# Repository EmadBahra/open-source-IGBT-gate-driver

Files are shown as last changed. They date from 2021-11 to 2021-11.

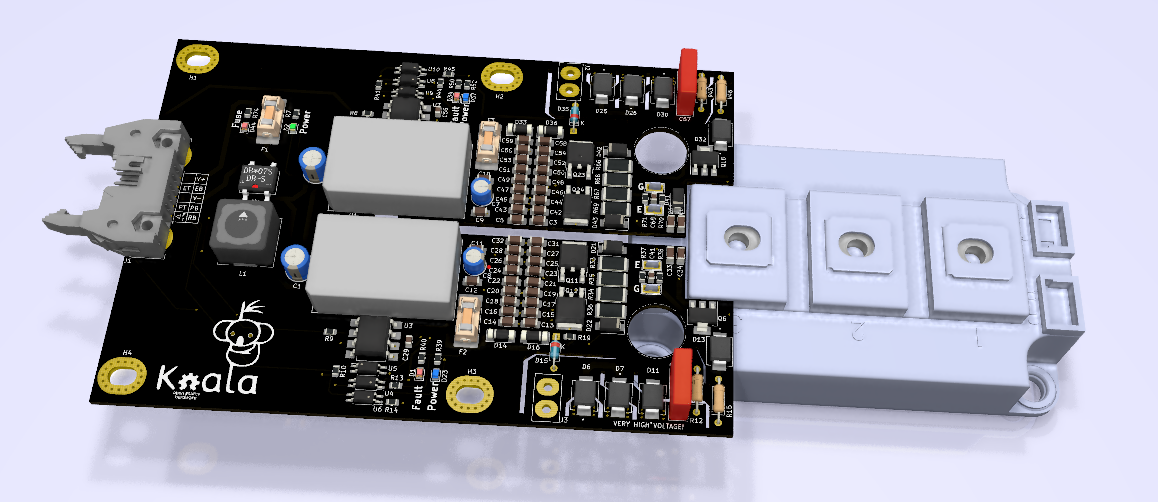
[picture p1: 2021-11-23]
Gate Driver.png

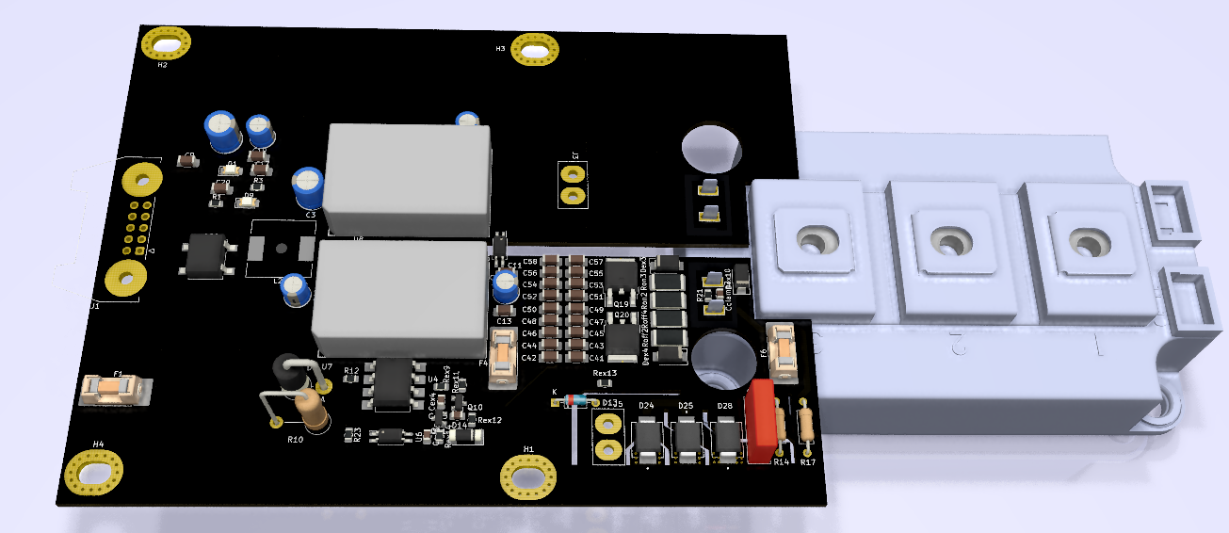
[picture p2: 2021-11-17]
halfway.png

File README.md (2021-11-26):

# Please read Wiki it will be complete ASAP
##  This is a beta version and it's not tested yet, so use it at your own risk under GPL v3 

##  Features
1. Short pulse suppression
2. Under voltage protection
3. Fault soft turn off
4. Active auto reset dynamic VCE clamp
5. Separate Ron and Roff
6. VCE monitoring
7. High side-Low side shoot thought protection (not tested yet)
8. Adjustable VCE protection
9. Mosfet gate clamp

## To add:
1. dynamic short-circuit protection
2. Designing its own converter

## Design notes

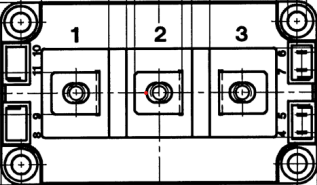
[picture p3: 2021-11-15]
skm200GB.png

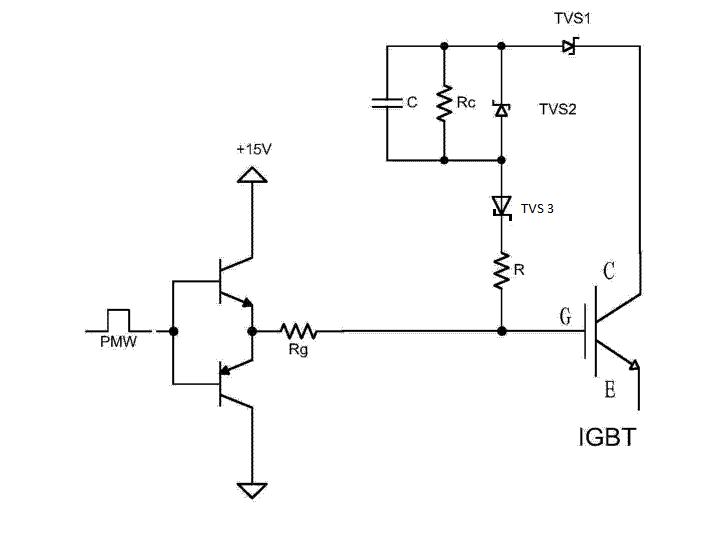
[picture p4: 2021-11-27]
WikiPics/Active Clamping.png

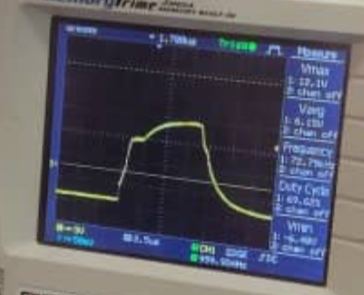
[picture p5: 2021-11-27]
WikiPics/VGE before claming.png

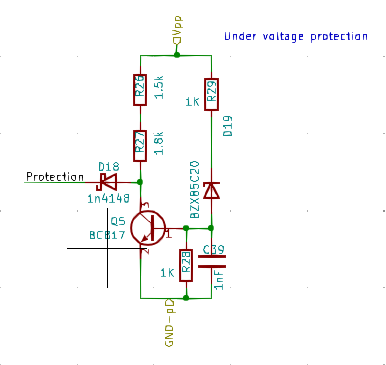
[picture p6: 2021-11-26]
WikiPics/Undervoltage.png

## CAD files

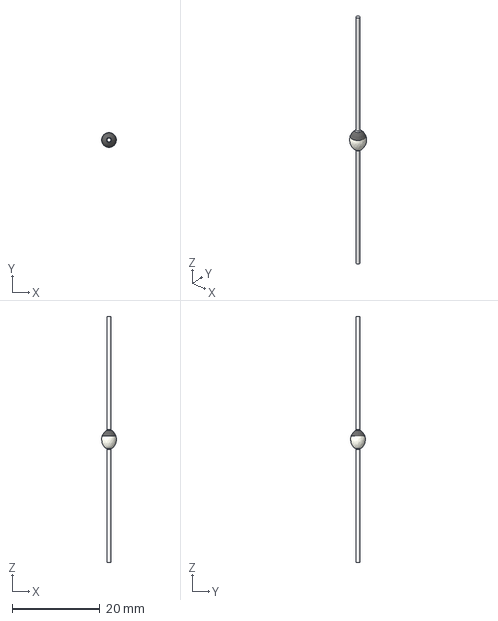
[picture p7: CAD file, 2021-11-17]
SOD-57_BYT62-BY203.stp
3.40 x 3.40 x 56.2 mm

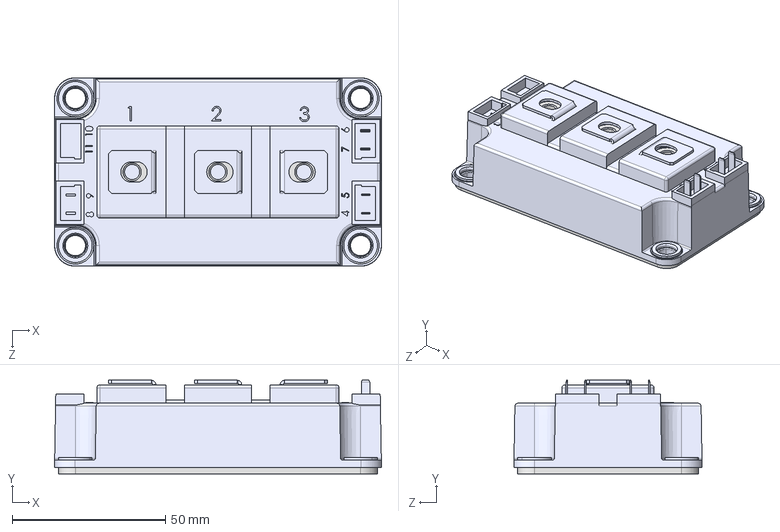
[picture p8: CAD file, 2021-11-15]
SEMIKRON_Semitrans_3_STEP.step
106.6 x 30.5 x 61.4 mm

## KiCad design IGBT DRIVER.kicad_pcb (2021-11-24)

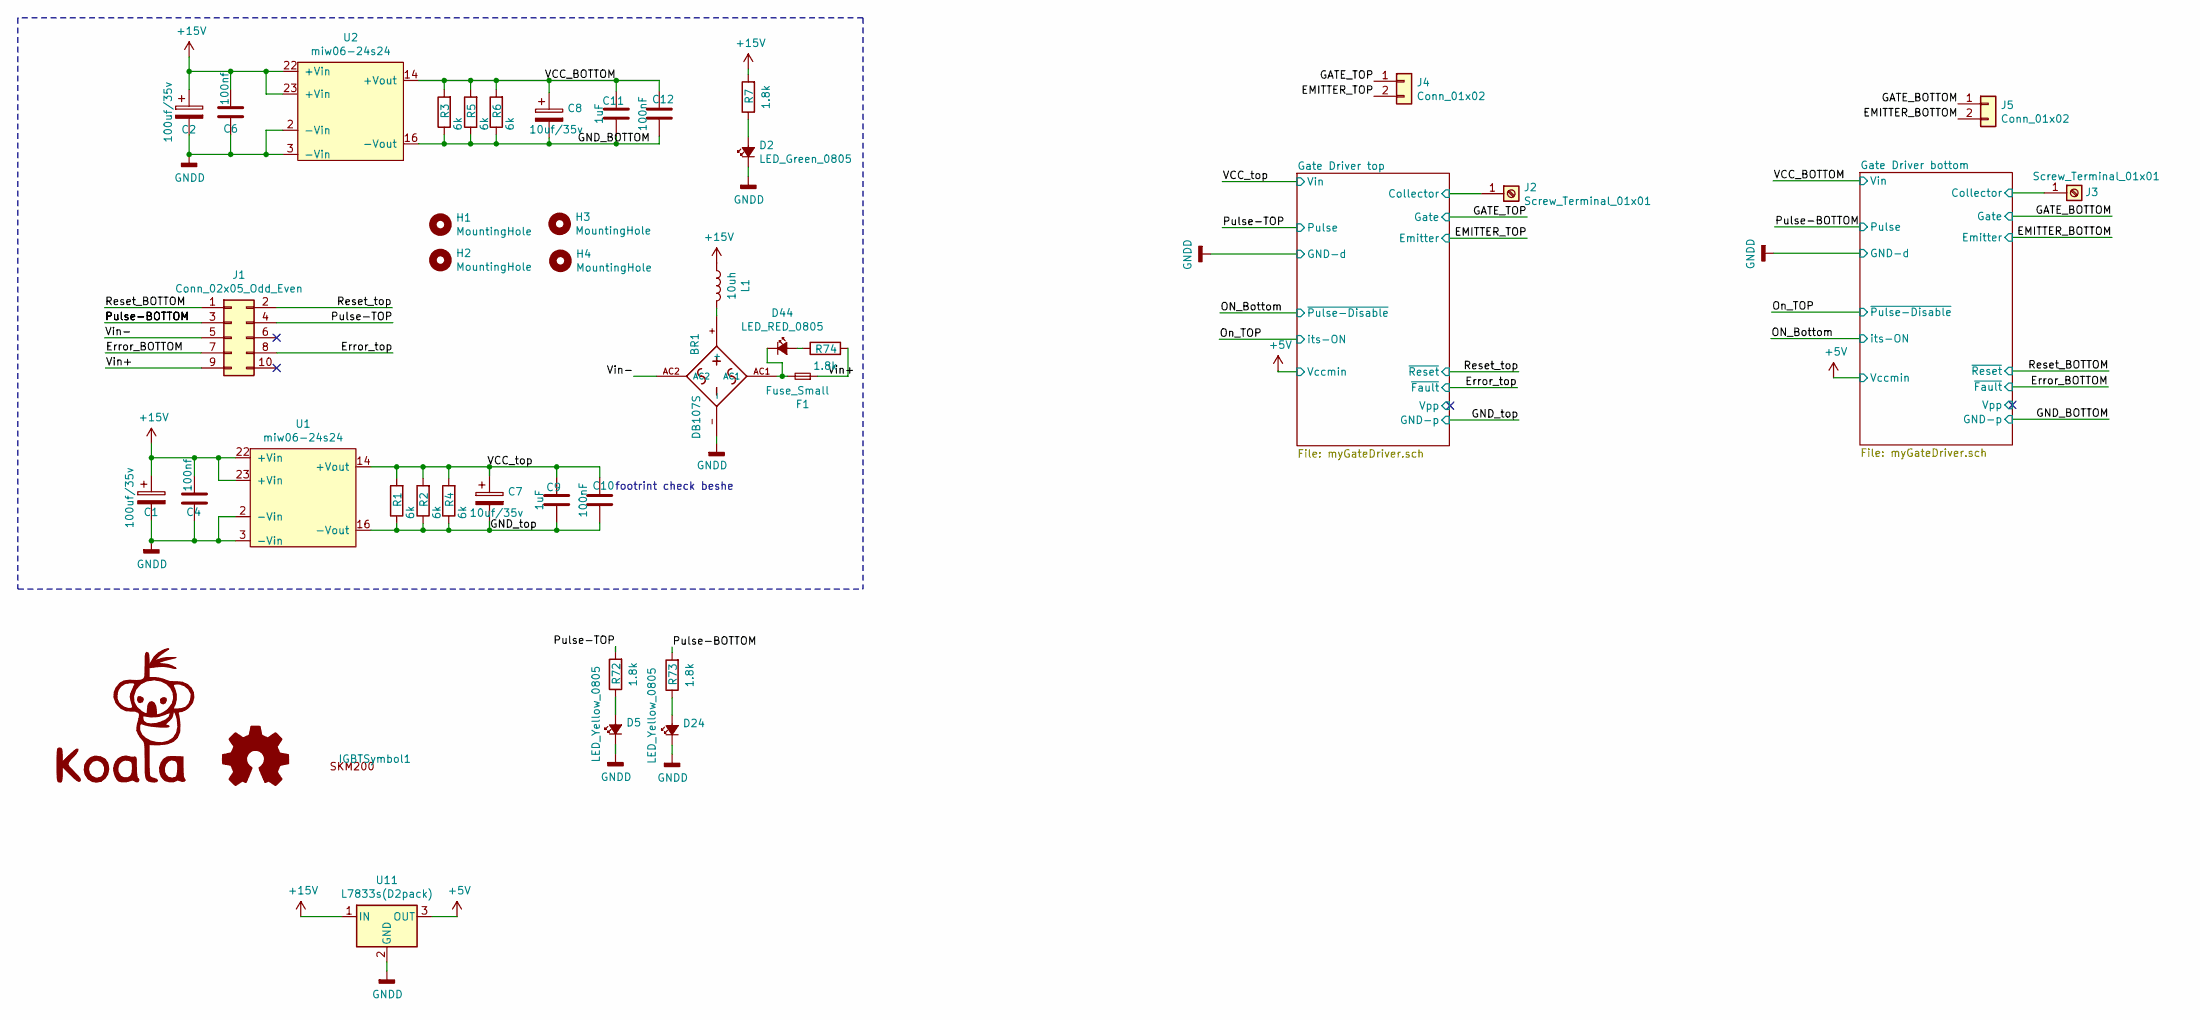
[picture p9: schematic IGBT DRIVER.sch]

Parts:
BR1: DB107S; DIOB_DB107S
C1, C2: 100uf/35v; CP_Radial_D6.3mm_P2.50mm
C4, C6: 100nf; C_1206_3216Metric_Pad1.33x1.80mm_HandSolder
C7, C8: 10uf/35v; CP_Radial_D5.0mm_P2.50mm
C9, C11: 1uF; C_1206_3216Metric_Pad1.33x1.80mm_HandSolder
C10, C12: 100nF; C_1206_3216Metric_Pad1.33x1.80mm_HandSolder
D2: LED_Green_0805
D5, D24: LED_Yellow_0805
D44: LED_RED_0805
F1: Fuse_Small; fuse.holder.1808
G1: LOGO; koalaLogo
H1, H2, H3, H4: MountingHole; MountingHole_4.3x6.2mm_M4_Pad_Via
IGBTSymbol1: SYM_Arrow45_Normal; skm200GB
J1: Conn_02x05_Odd_Even; IDC-Header_2x05-1MP_P2.54mm_Latch_Horizontal
J2, J3: Screw_Terminal_01x01; COOLERI
J4, J5: Conn_01x02; IGBT_Socket
L1: 10uh; L_12x12mm_H6mm
LOGO1: Logo_Open_Hardware_Small; OSHW-Logo_5.7x6mm_SilkScreen
R1, R2, R3, R4, R5, R6: 6k; R_1206_3216Metric
R7, R72, R73, R74: 1.8k; R_0805_2012Metric
U1, U2: miw06-24s24; MIWI06
U11: L7833s(D2pack); TO-263-3_TabPin2

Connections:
+5V: U11.3 (OUT); also elsewhere on the board
+15V: C1.1, C2.1, C4.2, C6.2, L1.1, R7.2, U1.22 (+Vin), U1.23 (+Vin), U2.22 (+Vin), U2.23 (+Vin), U11.1 (IN)
/EMITTER_BOTTOM: J5.2; also elsewhere on the board
/EMITTER_TOP: J4.2; also elsewhere on the board
/Error_BOTTOM: J1.7; also elsewhere on the board
/Error_top: J1.8; also elsewhere on the board
/GATE_BOTTOM: J5.1; also elsewhere on the board
/GATE_TOP: J4.1; also elsewhere on the board
/GND_BOTTOM: C8.2, C11.1, C12.1, R3.1, R5.1, R6.1, U2.16 (-Vout); also elsewhere on the board
/GND_top: C7.2, C9.1, C10.1, R1.1, R2.1, R4.1, U1.16 (-Vout); also elsewhere on the board
/Gate Driver bottom/Collector: J3.1; also elsewhere on the board
/Gate Driver top/Collector: J2.1; also elsewhere on the board
/Pulse-BOTTOM: J1.3, R73.2; also elsewhere on the board
/Pulse-TOP: J1.4, R72.2; also elsewhere on the board
/Reset_BOTTOM: J1.1; also elsewhere on the board
/Reset_top: J1.2; also elsewhere on the board
/VCC_BOTTOM: C8.1, C11.2, C12.2, R3.2, R5.2, R6.2, U2.14 (+Vout); also elsewhere on the board
/VCC_top: C7.1, C9.2, C10.2, R1.2, R2.2, R4.2, U1.14 (+Vout); also elsewhere on the board
/Vin+: F1.1, J1.9, R74.2
/Vin-: BR1.AC2, J1.5
GNDD: BR1.-, C1.2, C2.2, C4.1, C6.1, D2.1 (K), D5.1 (K), D24.1 (K), U1.2 (-Vin), U1.3 (-Vin), U2.2 (-Vin), U2.3 (-Vin), U11.2 (GND); also elsewhere on the board
unnamed: BR1.+, L1.2
unnamed: BR1.AC1, D44.1 (K), F1.2
unnamed: D2.2 (A), R7.1
unnamed: D5.2 (A), R72.1
unnamed: D24.2 (A), R73.1
unnamed: D44.2 (A), R74.1

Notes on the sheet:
footrint check beshe

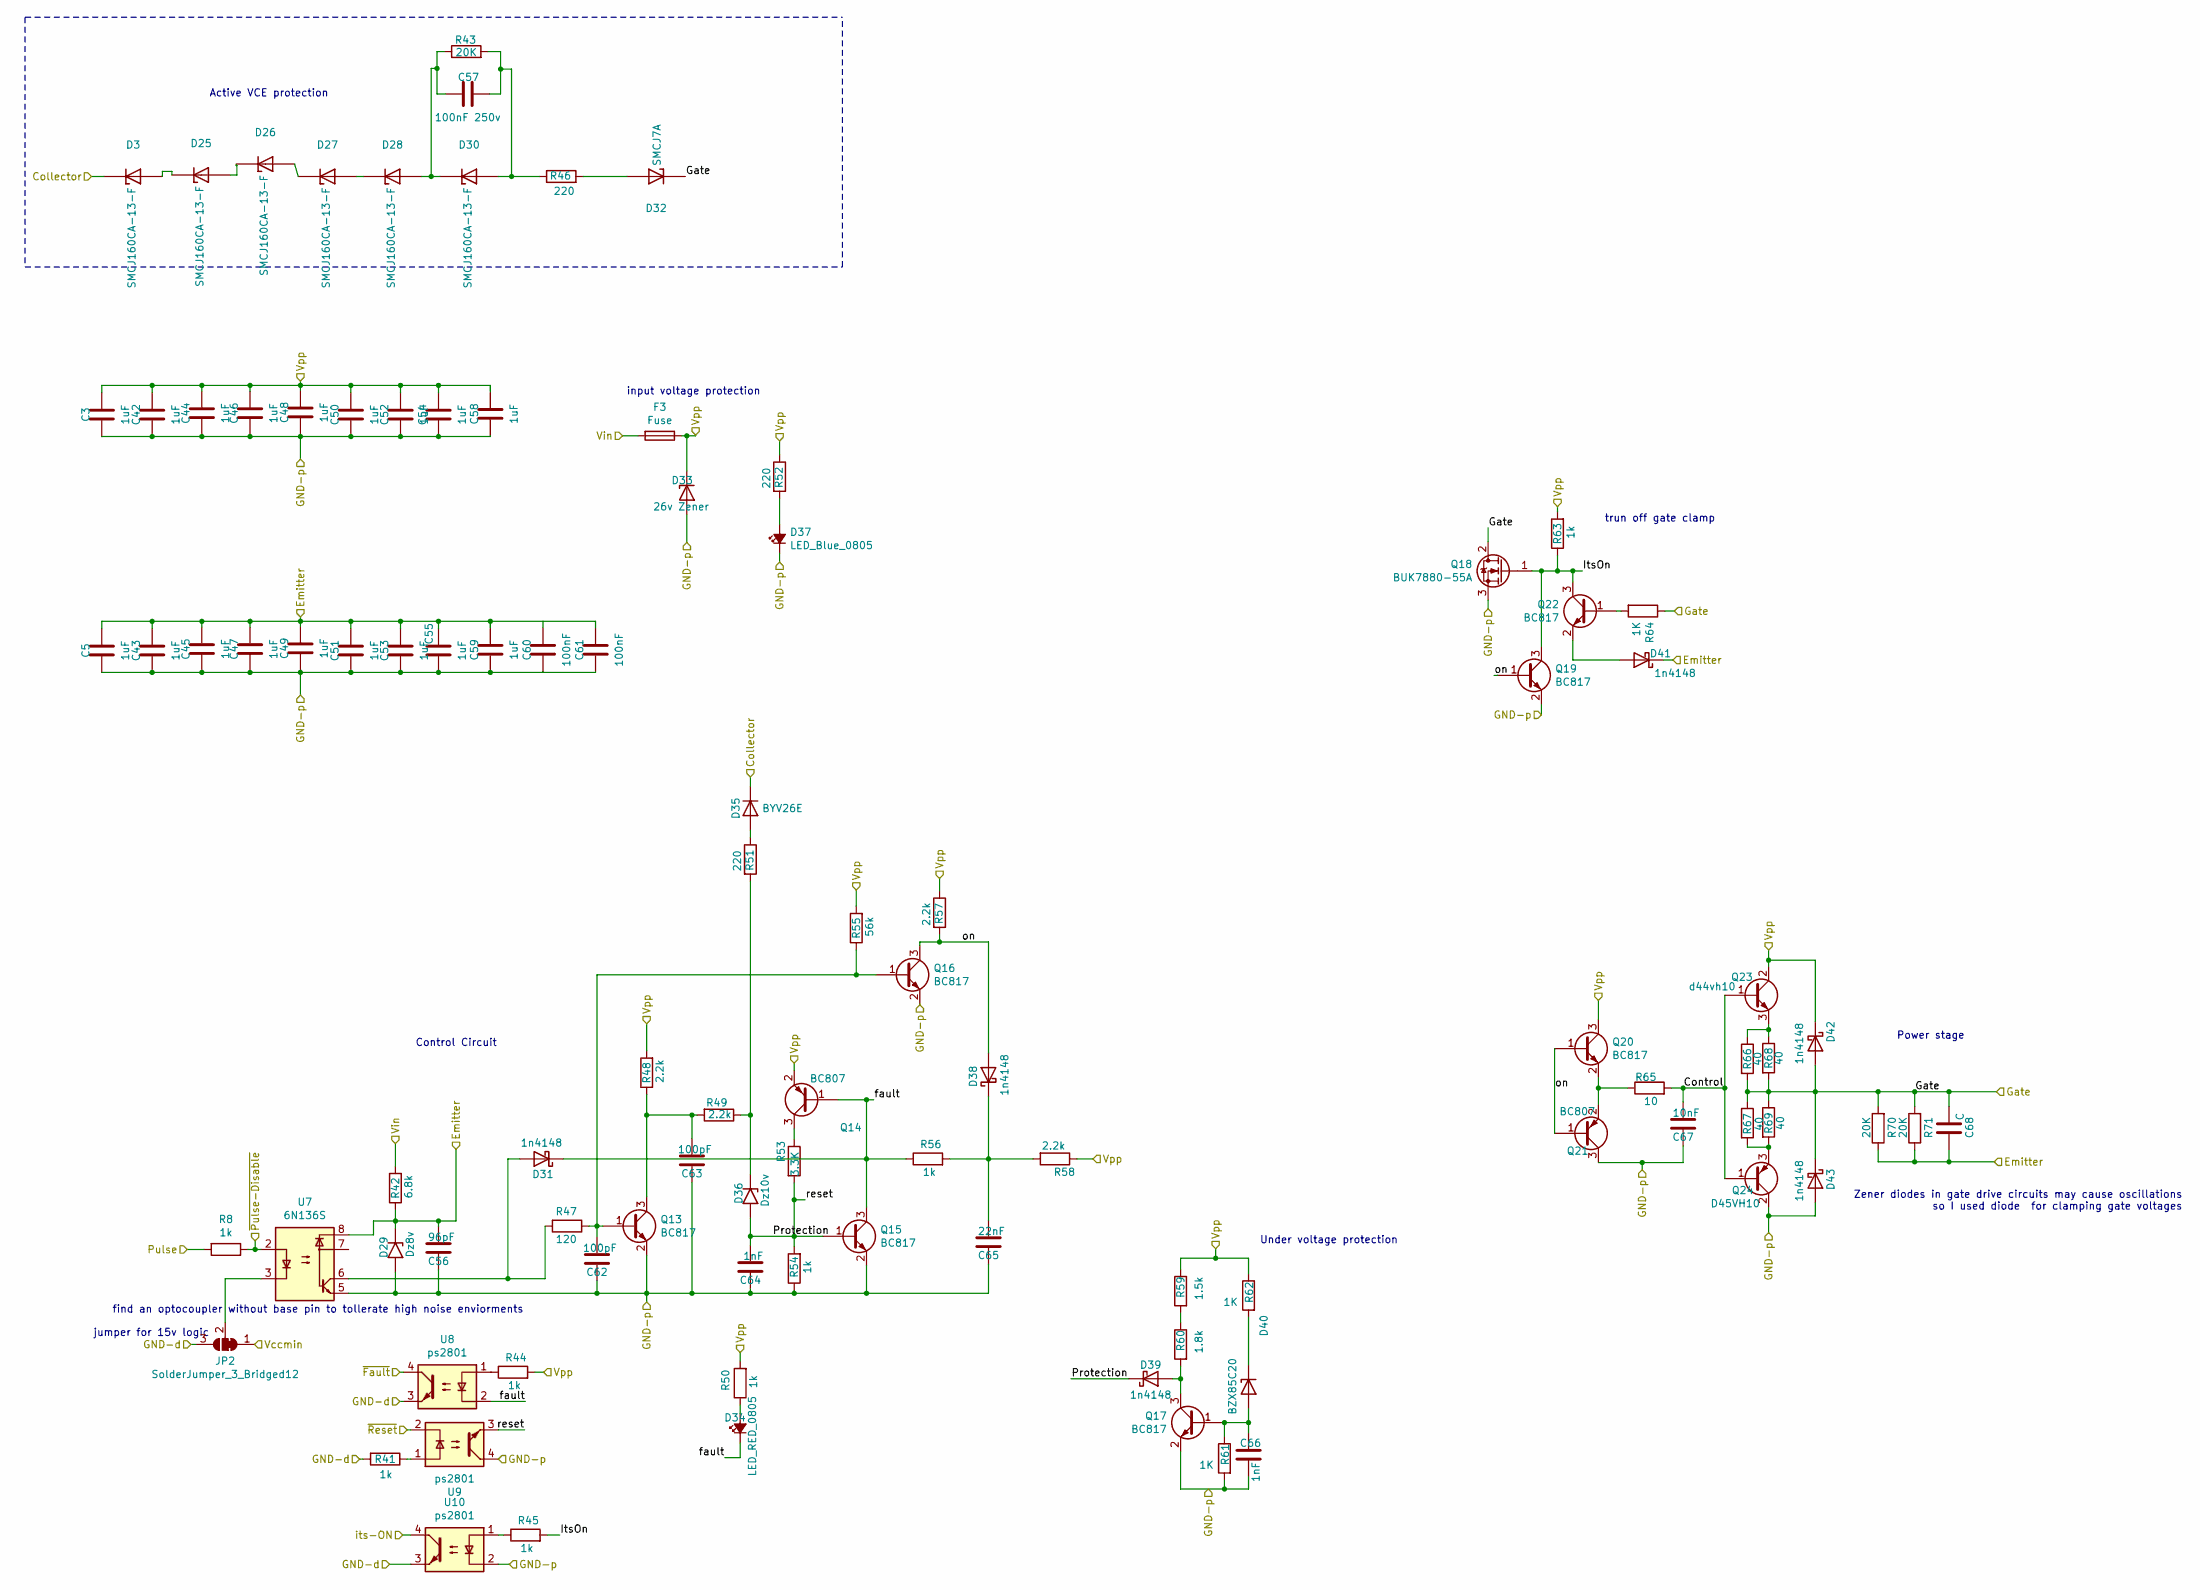
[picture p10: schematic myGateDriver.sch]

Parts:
C13, C14, C15, C16, C17, C18, C19, C20, C21, C22, C23, C24, C25, C26, C27, C28, C31, C32: 1uF; C_1206_3216Metric_Pad1.33x1.80mm_HandSolder
C29: 96pF; C_0805_2012Metric
C30: 100nF 250v; C_Rect_L13.0mm_W4.0mm_P10.00mm_FKS3_FKP3_MKS4
C33, C34: 100nF; C_1206_3216Metric_Pad1.33x1.80mm_HandSolder
C35, C36: 100pF; C_0805_2012Metric
C37: 1nF; C_0805_2012Metric
C38: 22nF; C_0805_2012Metric
C39: 1nF; C_1206_3216Metric_Pad1.33x1.80mm_HandSolder
C40: 10nF; C_0805_2012Metric
C41: C; C_0805_2012Metric
D1: LED_RED_0805
D4, D6, D7, D8, D9, D11: SMCJ160CA-13-F; DIOM7959X250N; PARTREV 5-2
D10: Dz8v; D_MELF
D12, D17, D18, D20, D21, D22: 1n4148; D_SMA
D13: SMCJ7A; DIOM7959X250N; PARTREV 5-2
D14: 26v Zener; D_MELF
D15: BYV26E; D_DO-35_SOD27_P7.62mm_Horizontal
D16: Dz10v; D_MELF
D19: BZX85C20; D_MELF
D23: LED_Blue_0805; LED_BLUE_0805
F2: Fuse; fuse.holder.1808
JP2: SolderJumper_3_Bridged12; SolderJumper-3_P1.3mm_Bridged2Bar12_Pad1.0x1.5mm
Q1, Q3, Q4, Q5, Q7, Q8, Q10: BC817; SOT-23
Q2, Q9: BC807; SOT-23
Q6: BUK7880-55A; SOT-223-3_TabPin2
Q11: d44vh10; TO-252-2
Q12: D45VH10; TO-252-2
R9, R10, R13, R14, R21, R23, R30, R40: 1k; R_0805_2012Metric
R11: 6.8k; R_0805_2012Metric
R12: 20K; R_Axial_DIN0207_L6.3mm_D2.5mm_P10.16mm_Horizontal
R15: 220; R_Axial_DIN0207_L6.3mm_D2.5mm_P10.16mm_Horizontal
R16: 120; R_0805_2012Metric
R17, R18, R24, R25: 2.2k; R_0805_2012Metric
R19, R39: 220; R_0805_2012Metric
R20: 3.3K; R_0805_2012Metric
R22: 56k; R_0805_2012Metric
R26: 1.5k; R_0805_2012Metric
R27: 1.8k; R_0805_2012Metric
R28, R29, R31: 1K; R_0805_2012Metric
R32: 10; R_0805_2012Metric
R33, R34, R35, R36: 40; R_2512_6332Metric
R37, R38: 20K; R_0805_2012Metric
U3: 6N136S; SMDIP-8_W9.53mm
U4, U5, U6: ps2801; SOP-4_4.4x2.6mm_P1.27mm

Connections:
+5V: JP2.1 (A); also elsewhere on the board
/EMITTER_BOTTOM: C14.2, C16.2, C18.2, C20.2, C22.2, C24.2, C26.2, C28.2, C29.2, C32.2, C33.2, C34.2, C41.1, D10.1 (A1), D20.1 (K), R11.1, R37.1, R38.1, U3.8; also elsewhere on the board
/Error_BOTTOM: U4.4; also elsewhere on the board
/GATE_BOTTOM: C41.2, D13.C, D21.2 (A), D22.1 (K), Q6.2 (D), R31.1, R33.2, R34.1, R35.2, R36.1, R37.2, R38.2; also elsewhere on the board
/GND_BOTTOM: C13.1, C14.1, C15.1, C16.1, C17.1, C18.1, C19.1, C20.1, C21.1, C22.1, C23.1, C24.1, C25.1, C26.1, C27.1, C28.1, C29.1, C31.1, C32.1, C33.1, C34.1, C35.1, C36.1, C37.1, C38.1, C39.2, C40.1, D10.2 (A2), D14.2 (A), D22.2 (A), D23.1 (K), Q1.2 (E), Q3.2 (E), Q4.2 (E), Q5.2 (E), Q6.3 (S), Q7.2 (E), Q9.3 (C), Q12.2 (C), R21.1, R28.2, U3.5, U5.4, U6.2; also elsewhere on the board
/Gate Driver bottom/Collector: D4.C, D15.2 (K); also elsewhere on the board
/Gate Driver bottom/Control: C40.2, Q11.1 (B), Q12.1 (B), R32.2
/Gate Driver bottom/ItsOn: Q6.1 (G), Q7.3 (C), Q10.3 (C), R14.2, R30.1
/Gate Driver bottom/Protection: C37.2, D16.2 (A2), D18.1 (K), Q3.1 (B), R20.2, R21.2, U5.3
/Gate Driver bottom/Vpp: C13.2, C15.2, C17.2, C19.2, C21.2, C23.2, C25.2, C27.2, C31.2, D14.1 (K), D21.1 (K), F2.1, Q2.2 (E), Q8.3 (C), Q11.2 (C), R13.2, R17.2, R22.2, R24.1, R25.1, R26.1, R29.1, R30.2, R39.1, R40.2
/Gate Driver bottom/fault: D1.1 (K), D12.1 (K), Q2.1 (B), Q3.3 (C), R23.1, U4.2
/Gate Driver bottom/on: D17.2 (A), Q4.3 (C), Q7.1 (B), Q8.1 (B), Q9.1 (B), R24.2
/ON_Bottom: U6.4; also elsewhere on the board
/On_TOP: R9.1, U3.2; also elsewhere on the board
/Pulse-BOTTOM: R9.2; also elsewhere on the board
/Reset_BOTTOM: U5.2; also elsewhere on the board
/VCC_BOTTOM: F2.2, R11.2; also elsewhere on the board
GNDD: JP2.3 (B), R10.2, U4.3, U6.3; also elsewhere on the board
unnamed: C30.1, D9.A, D11.C, R12.1
unnamed: C30.2, D11.A, R12.2, R15.1
unnamed: C35.2, Q1.1 (B), Q4.1 (B), R16.1, R22.1
unnamed: C36.2, Q1.3 (C), R17.1, R18.2
unnamed: C38.2, D17.1 (K), R23.2, R25.2
unnamed: C39.1, D19.2 (A), Q5.1 (B), R28.1
unnamed: D1.2 (A), R40.1
unnamed: D4.A, D6.C
unnamed: D6.A, D7.C
unnamed: D7.A, D8.C
unnamed: D8.A, D9.C
unnamed: D12.2 (A), R16.2, U3.6
unnamed: D13.A, R15.2
unnamed: D15.1 (A), R19.1
unnamed: D16.1 (A1), R18.1, R19.2
unnamed: D18.2 (A), Q5.3 (C), R27.2
unnamed: D19.1 (K), R29.2
unnamed: D20.2 (A), Q10.2 (E)
unnamed: D23.2 (A), R39.2
unnamed: Q2.3 (C), R20.1
unnamed: Q8.2 (E), Q9.2 (E), R32.1
unnamed: Q10.1 (B), R31.2
unnamed: Q11.3 (E), R33.1, R35.1
unnamed: Q12.3 (E), R34.2, R36.2
unnamed: R10.1, U5.1
unnamed: R13.1, U4.1
unnamed: R14.1, U6.1
unnamed: R26.2, R27.1

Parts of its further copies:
C3, C5, C42, C43, C44, C45, C46, C47, C48, C49, C50, C51, C52, C53, C54, C55, C58, C59: 1uF; C_1206_3216Metric_Pad1.33x1.80mm_HandSolder
C56: 96pF; C_0805_2012Metric
C57: 100nF 250v; C_Rect_L13.0mm_W4.0mm_P10.00mm_FKS3_FKP3_MKS4
C60, C61: 100nF; C_1206_3216Metric_Pad1.33x1.80mm_HandSolder
C62, C63: 100pF; C_0805_2012Metric
C64: 1nF; C_0805_2012Metric
C65: 22nF; C_0805_2012Metric
C66: 1nF; C_1206_3216Metric_Pad1.33x1.80mm_HandSolder
C67: 10nF; C_0805_2012Metric
C68: C; C_0805_2012Metric
D3, D25, D26, D27, D28, D30: SMCJ160CA-13-F; DIOM7959X250N; PARTREV 5-2
D29: Dz8v; D_MELF
D31, D38, D39, D41, D42, D43: 1n4148; D_SMA
D32: SMCJ7A; DIOM7959X250N; PARTREV 5-2
D33: 26v Zener; D_MELF
D34: LED_RED_0805
D35: BYV26E; D_DO-35_SOD27_P7.62mm_Horizontal
D36: Dz10v; D_MELF
D37: LED_Blue_0805; LED_BLUE_0805
D40: BZX85C20; D_MELF
F3: Fuse; fuse.holder.1808
JP1: SolderJumper_3_Bridged12; SolderJumper-3_P1.3mm_Bridged2Bar12_Pad1.0x1.5mm
Q13, Q15, Q16, Q17, Q19, Q20, Q22: BC817; SOT-23
Q14, Q21: BC807; SOT-23
Q18: BUK7880-55A; SOT-223-3_TabPin2
Q23: d44vh10; TO-252-2
Q24: D45VH10; TO-252-2
R8, R41, R44, R45, R50, R54, R56, R63: 1k; R_0805_2012Metric
R42: 6.8k; R_0805_2012Metric
R43: 20K; R_Axial_DIN0207_L6.3mm_D2.5mm_P10.16mm_Horizontal
R46: 220; R_Axial_DIN0207_L6.3mm_D2.5mm_P10.16mm_Horizontal
R47: 120; R_0805_2012Metric
R48, R49, R57, R58: 2.2k; R_0805_2012Metric
R51, R52: 220; R_0805_2012Metric
R53: 3.3K; R_0805_2012Metric
R55: 56k; R_0805_2012Metric
R59: 1.5k; R_0805_2012Metric
R60: 1.8k; R_0805_2012Metric
R61, R62, R64: 1K; R_0805_2012Metric
R65: 10; R_0805_2012Metric
R66, R67, R68, R69: 40; R_2512_6332Metric
R70, R71: 20K; R_0805_2012Metric
U7: 6N136S; SMDIP-8_W9.53mm
U8, U9, U10: ps2801; SOP-4_4.4x2.6mm_P1.27mm

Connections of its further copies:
+5V: JP1.1 (A); also elsewhere on the board
/EMITTER_TOP: C5.2, C43.2, C45.2, C47.2, C49.2, C51.2, C53.2, C55.2, C56.2, C59.2, C60.2, C61.2, C68.1, D29.1 (A1), D41.1 (K), R42.1, R70.1, R71.1, U7.8; also elsewhere on the board
/Error_top: U8.4; also elsewhere on the board
/GATE_TOP: C68.2, D32.C, D42.2 (A), D43.1 (K), Q18.2 (D), R64.1, R66.2, R67.1, R68.2, R69.1, R70.2, R71.2; also elsewhere on the board
/GND_top: C3.1, C5.1, C42.1, C43.1, C44.1, C45.1, C46.1, C47.1, C48.1, C49.1, C50.1, C51.1, C52.1, C53.1, C54.1, C55.1, C56.1, C58.1, C59.1, C60.1, C61.1, C62.1, C63.1, C64.1, C65.1, C66.2, C67.1, D29.2 (A2), D33.2 (A), D37.1 (K), D43.2 (A), Q13.2 (E), Q15.2 (E), Q16.2 (E), Q17.2 (E), Q18.3 (S), Q19.2 (E), Q21.3 (C), Q24.2 (C), R54.1, R61.2, U7.5, U9.4, U10.2; also elsewhere on the board
/Gate Driver top/Collector: D3.C, D35.2 (K); also elsewhere on the board
/Gate Driver top/Control: C67.2, Q23.1 (B), Q24.1 (B), R65.2
/Gate Driver top/ItsOn: Q18.1 (G), Q19.3 (C), Q22.3 (C), R45.2, R63.1
/Gate Driver top/Protection: C64.2, D36.2 (A2), D39.1 (K), Q15.1 (B), R53.2, R54.2, U9.3
/Gate Driver top/Vpp: C3.2, C42.2, C44.2, C46.2, C48.2, C50.2, C52.2, C54.2, C58.2, D33.1 (K), D42.1 (K), F3.1, Q14.2 (E), Q20.3 (C), Q23.2 (C), R44.2, R48.2, R50.2, R52.1, R55.2, R57.1, R58.1, R59.1, R62.1, R63.2
/Gate Driver top/fault: D31.1 (K), D34.1 (K), Q14.1 (B), Q15.3 (C), R56.1, U8.2
/Gate Driver top/on: D38.2 (A), Q16.3 (C), Q19.1 (B), Q20.1 (B), Q21.1 (B), R57.2
/ON_Bottom: R8.1, U7.2; also elsewhere on the board
/On_TOP: U10.4; also elsewhere on the board
/Pulse-TOP: R8.2; also elsewhere on the board
/Reset_top: U9.2; also elsewhere on the board
/VCC_top: F3.2, R42.2; also elsewhere on the board
GNDD: JP1.3 (B), R41.2, U8.3, U10.3; also elsewhere on the board
unnamed: C57.1, D28.A, D30.C, R43.1
unnamed: C57.2, D30.A, R43.2, R46.1
unnamed: C62.2, Q13.1 (B), Q16.1 (B), R47.1, R55.1
unnamed: C63.2, Q13.3 (C), R48.1, R49.2
unnamed: C65.2, D38.1 (K), R56.2, R58.2
unnamed: C66.1, D40.2 (A), Q17.1 (B), R61.1
unnamed: D25.A, D26.C
unnamed: D3.A, D25.C
unnamed: D26.A, D27.C
unnamed: D27.A, D28.C
unnamed: D31.2 (A), R47.2, U7.6
unnamed: D32.A, R46.2
unnamed: D34.2 (A), R50.1
unnamed: D35.1 (A), R51.1
unnamed: D36.1 (A1), R49.1, R51.2
unnamed: D37.2 (A), R52.2
unnamed: D39.2 (A), Q17.3 (C), R60.2
unnamed: D40.1 (K), R62.2
unnamed: D41.2 (A), Q22.2 (E)
unnamed: Q14.3 (C), R53.1
unnamed: Q20.2 (E), Q21.2 (E), R65.1
unnamed: Q22.1 (B), R64.2
unnamed: Q23.3 (E), R66.1, R68.1
unnamed: Q24.3 (E), R67.2, R69.2
unnamed: R41.1, U9.1
unnamed: R44.1, U8.1
unnamed: R45.1, U10.1
unnamed: R59.2, R60.1

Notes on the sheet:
Zener diodes in gate drive circuits may cause oscillations so I used diode for clamping gate voltages
Active VCE protection
input voltage protection
trun off gate clamp
Under voltage protection
Power stage
Control Circuit
find an optocoupler without base pin to tollerate high noise enviorments
jumper for 15v logic

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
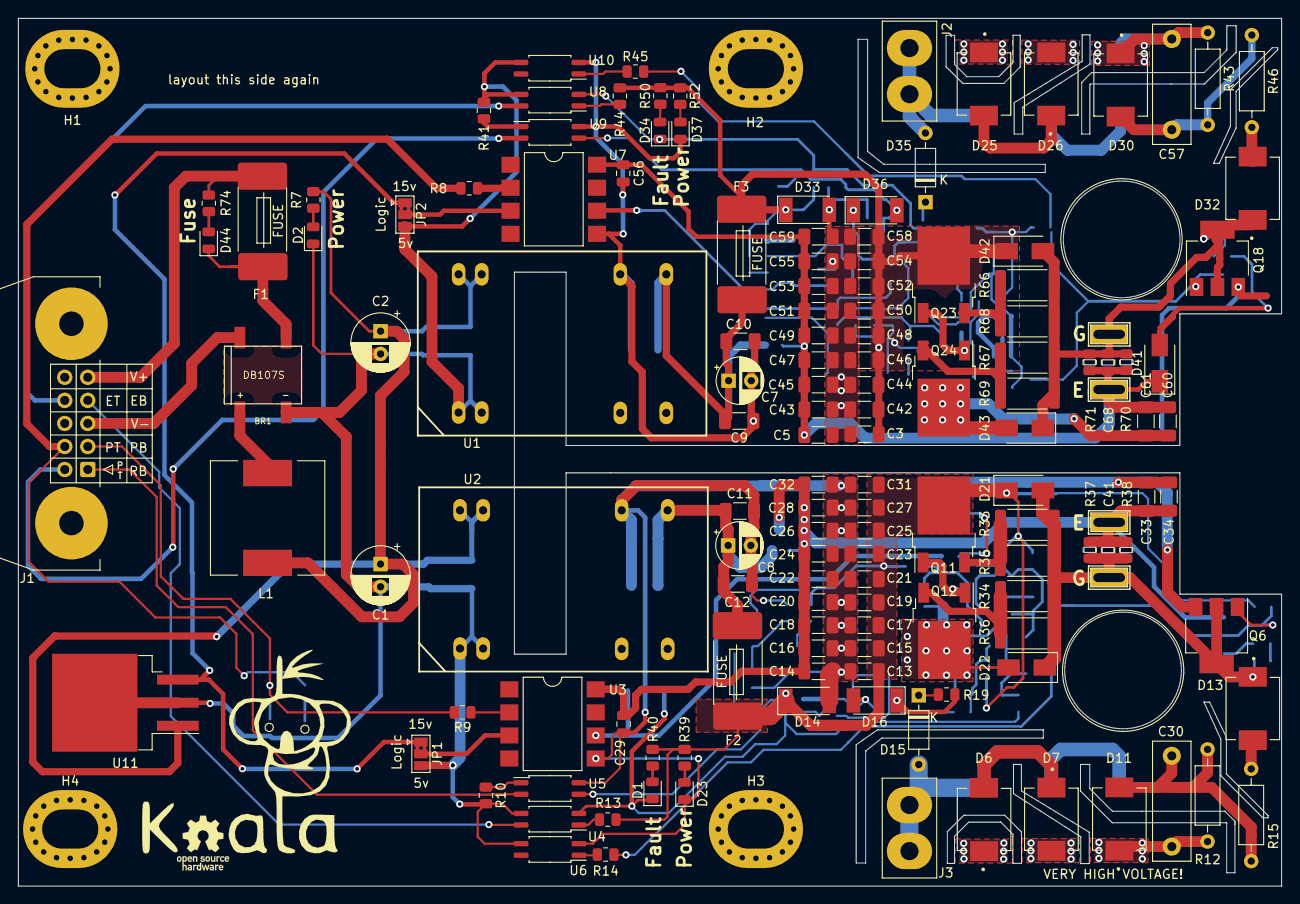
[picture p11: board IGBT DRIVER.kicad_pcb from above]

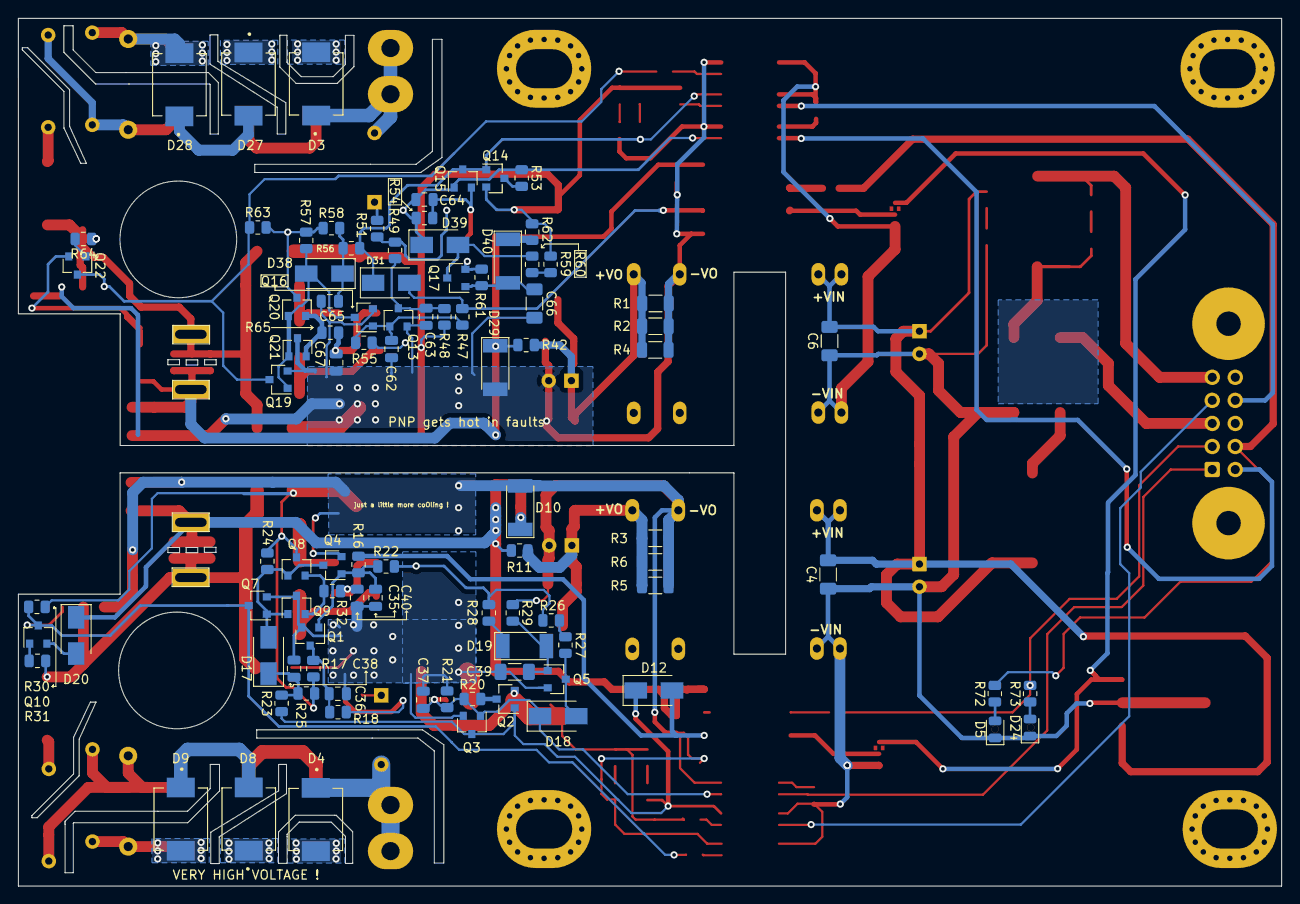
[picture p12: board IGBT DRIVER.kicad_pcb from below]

Board: 2 copper layers, 139.2 x 95.6 mm, 240 parts (94 on the bottom side), 99 nets.

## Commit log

2021-11-15 fuse added
    [myGateDriver.sch]
2021-11-15 skm200 layout added
    [IGBT DRIVER.kicad_pcb]
2021-11-15 skm200 3d
    [IGBT DRIVER.kicad_pcb, IGBT DRIVER.sch, SEMIKRON_Semitrans_3_STEP.step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]
2021-11-16 changed bjt
    [IGBT DRIVER.kicad_pcb, IGBT DRIVER.sch, myGateDriver.sch]
2021-11-16 some placement
    [IGBT DRIVER.kicad_pcb, IGBT DRIVER.sch, myGateDriver.sch]
2021-11-17 some placements have done
    [IGBT DRIVER.kicad_pcb, IGBT DRIVER.sch, SOD-57_BYT62-BY203.stp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]
2021-11-18 placing back of bottom
    [IGBT DRIVER.kicad_pcb, IGBT DRIVER.sch, myGateDriver.sch]
2021-11-22 added top parts
    [IGBT DRIVER.kicad_pcb, IGBT DRIVER.sch, myGateDriver.sch]
2021-11-23 topside added
    [IGBT DRIVER.kicad_pcb, IGBT DRIVER.sch, myGateDriver.sch]
2021-11-23 Create Gate Driver.png
2021-11-24 BOM added
2021-11-24 15v logic added
    [IGBT DRIVER.sch, myGateDriver.sch]
2021-11-26 add some wiki pics
    [IGBT DRIVER.kicad_pcb]
2021-11-26 under voltage picture for wiki
2021-11-26 soft shutdown wiki pic added
    [myGateDriver.sch]
2021-11-27 Create Active Clamping.png
2021-11-27 Create active clamp2.png
2021-11-27 clamping pictures
2021-11-27 clamping video added
